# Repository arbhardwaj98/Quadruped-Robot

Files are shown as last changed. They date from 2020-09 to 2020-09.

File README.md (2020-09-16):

# Quadruped-Robot

### A Low Cost Quadruped Robot with Autonomous Capabilities

The aim was to develop a low cost quadruped robot so that it has the capability to traverse autonomously on irregular terrains:

1) The quadruped was designed employing the 5bar - 5R mechanism, allowing us to mount all the actuators on the chassis of the robot, thus minimizing the moment of inertia of the leg. 
2) Carbon Fibre Reinforced Polymer tubes were used for manufacturing the links of the mechanism to keep it feather light. By using appropriate materials and other weight reduction techniques we were able to limit the weight of the robot to 1.15 kg.
3) Stress analysis of the various mechanical components of the robot to prevent failures. Material Optimizations were implemented to reduce weight and strengthen the components.
4) ROS was integrated with the robot, after developing the URDF of the 5bar - 5R closed chain. Then ROS controllers on each of the eight actuators were set up to achieve the joint control. 
5) Stereo Camera and IMU sensors were integrated with the robot in the simulation. Extended Kalman Filtering was used for the fusion of the two sensor data to produce a much accurate odometry.
6) Equations of motion were derived for the robot A base controllers was developed to provide movement to the toe and to generate the various types of motion given the command velocity.
7) Tested using Gazebo based physics simulation for the robot, to validate the equations derived, check robot stability and to test the efficiency of the base controller.

Find more information about the robot [here](https://drive.google.com/file/d/16AhPm6JRH62gSZBvzB-JlDFh6qmGrHIq/view?usp=sharing).

Check out the [videos](https://drive.google.com/drive/folders/1-zKFX-dxUtHMzNQqa7gvRL7YORVA8Zfu?usp=sharing) of the prototype and simulation.

## Includes:

1) Description Files
2) Gazebo Simulation Package
3) ROS Control Package
4) Hardware Drivers
5) Matlab Codes for Trajectory Generation
6) CAD Files

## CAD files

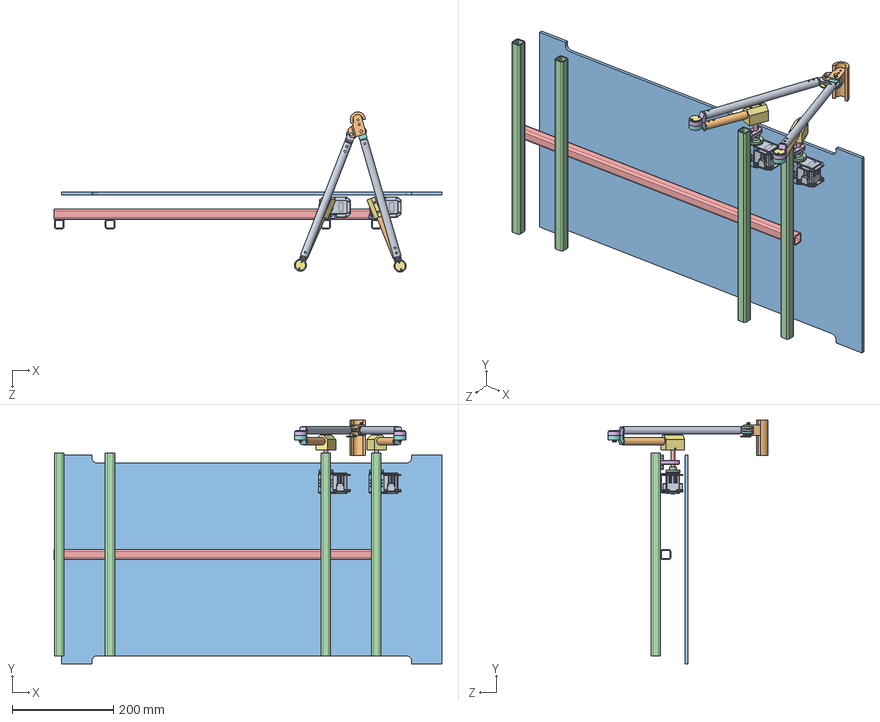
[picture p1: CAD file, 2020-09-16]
CAD/Minitaur1.4/assembly.SLDASM
764.9 x 480.8 x 315.8 mm
ncoupler x 2
ncrank x 2
Channel_2
Channel_1
joint_part_2 x 2
joint_part_3 x 4
joint_part_4 x 2
Dynamixel_64T x 2
Dynamixel_64T_servohorn x 2
Dynamixel_FR05-S101K x 2
motor_shaft_hub1 x 2
motor_shaft x 2
bearing_housing x 2
motor_shaft_hub2 x 2
joint_bottom_part_2
joint_part_1
toe

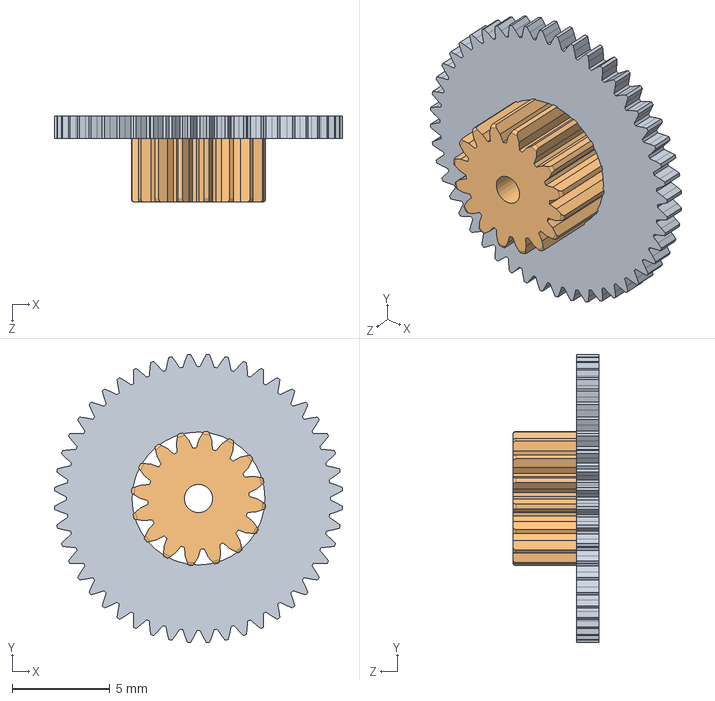
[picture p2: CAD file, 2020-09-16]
CAD/Minitaur1.4/egrane3aluminiolaton.SLDPRT.SLDASM
14.7 x 14.7 x 4.40 mm
egrane3laton
egrane3aluminio

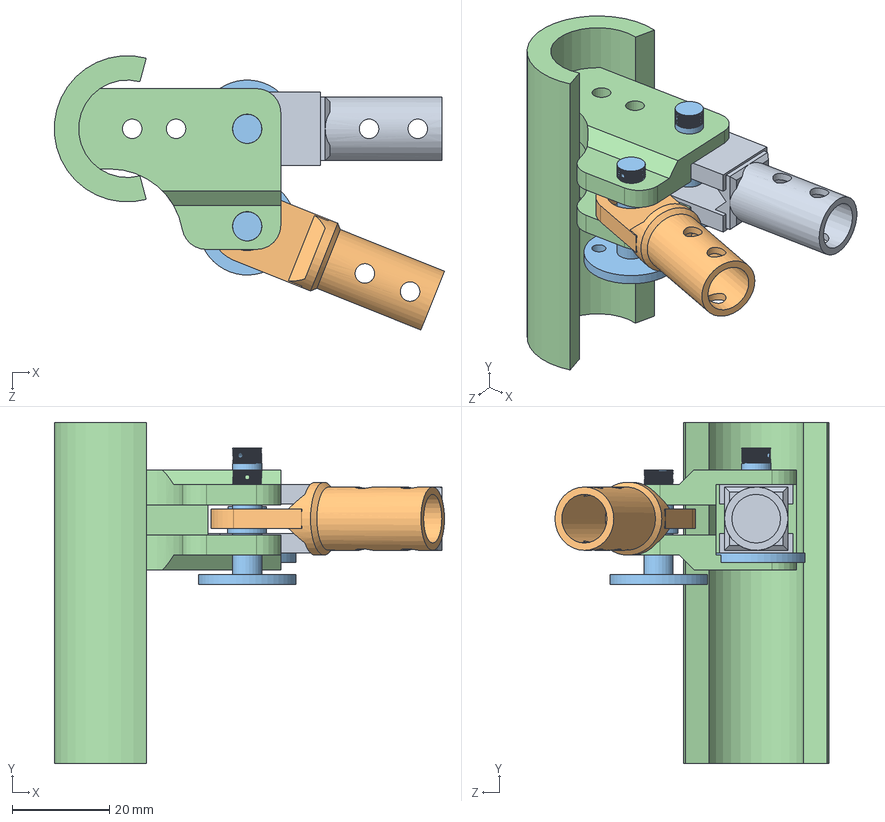
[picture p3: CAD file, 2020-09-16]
CAD/Minitaur1.4/Joint_Bottom_Assembly.SLDASM
80.0 x 70.0 x 56.2 mm
joint_bottom_part_2
joint_part_1
toe
joint_part_3

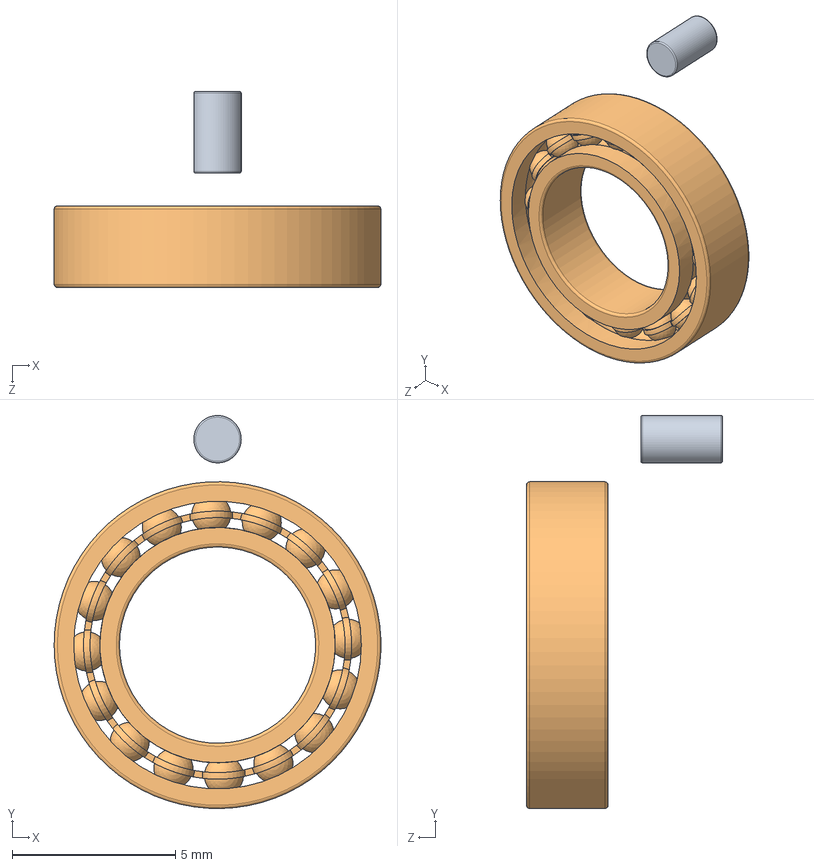
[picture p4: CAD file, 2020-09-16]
CAD/Minitaur1.4/egrane2latonpin.SLDPRT.SLDASM
10.00 x 12.0 x 6.00 mm
egrane2latonpin
radial ball bearing_68_am

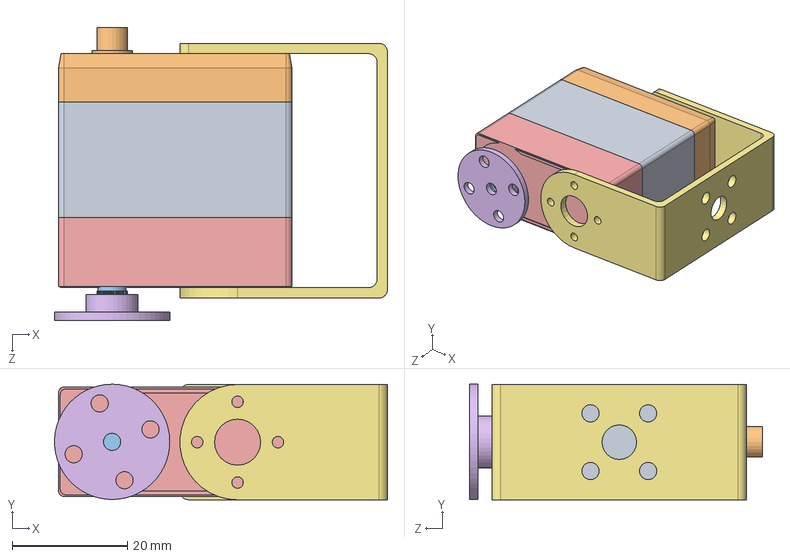
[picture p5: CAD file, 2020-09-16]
CAD/Minitaur1.4/servo.SLDASM
57.7 x 20.1 x 50.8 mm
centroservo
egrane3laton
egrane3aluminio
egrane4laton
egrane4aluminio
engrane2
pincorto
pinlargo
radial ball bearing_68_am x 2
baseservo
otro
egrane2latonpin
tapa servo
Bracket-Horn
mount

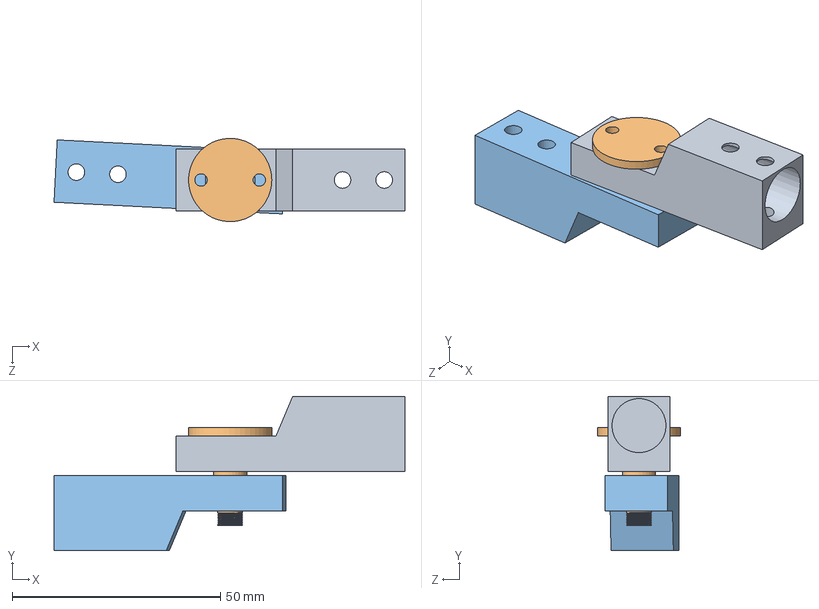
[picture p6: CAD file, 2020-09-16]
CAD/Minitaur1.4/Joint_Assembly.SLDASM
84.3 x 37.0 x 20.0 mm
joint_part_2
joint_part_3
joint_part_5

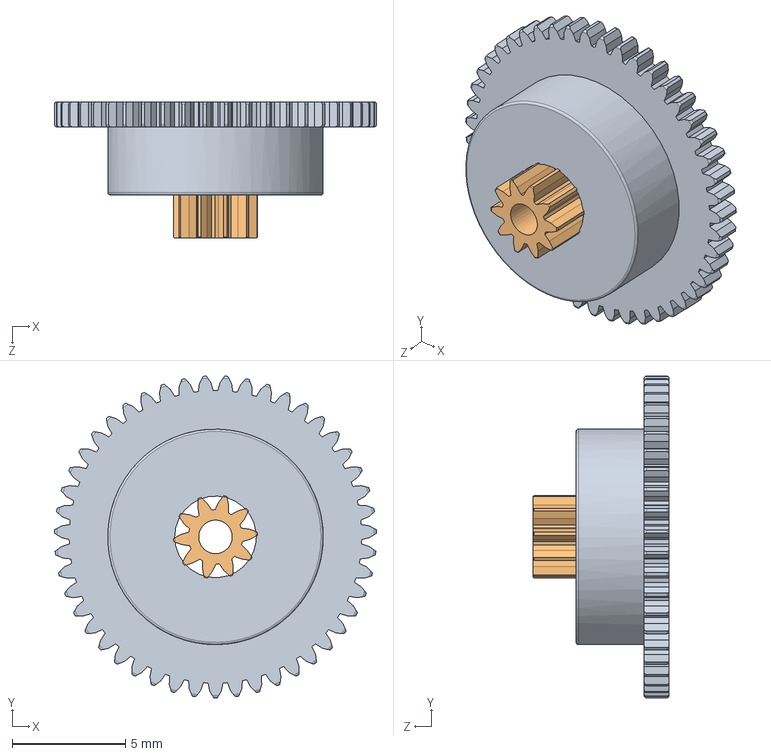
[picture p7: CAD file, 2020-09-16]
CAD/Minitaur1.4/egrane4aluminiolaton.SLDPRT.SLDASM
14.2 x 14.2 x 6.00 mm
egrane4laton
egrane4aluminio

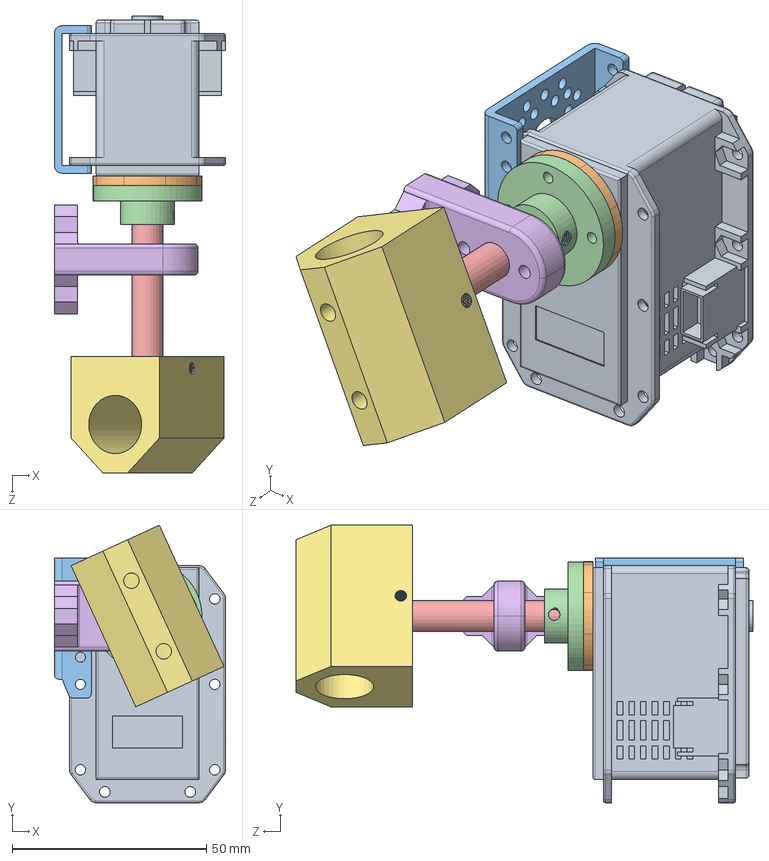
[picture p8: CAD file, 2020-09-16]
CAD/Minitaur1.4/Dynamixel_assem.SLDASM
44.1 x 71.5 x 117.7 mm
Dynamixel_64T
Dynamixel_64T_servohorn
Dynamixel_FR05-S101K
motor_shaft_hub1
motor_shaft
bearing_housing
motor_shaft_hub2

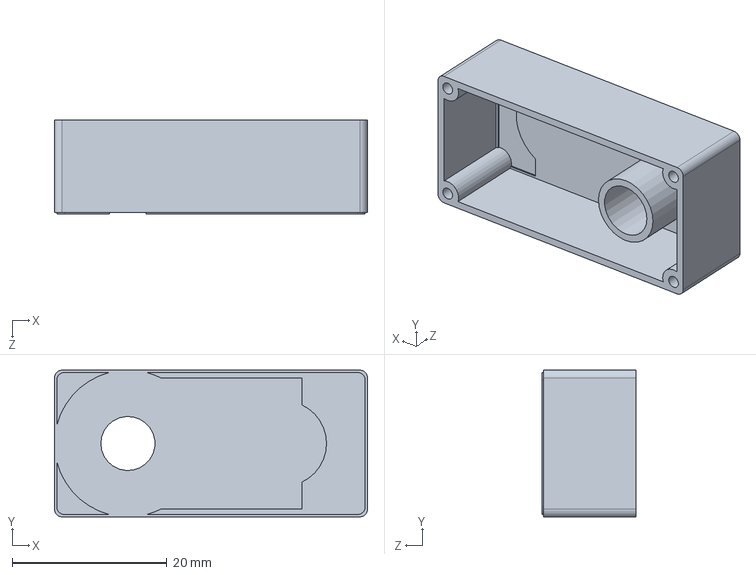
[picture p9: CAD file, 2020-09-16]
CAD/Minitaur1.4/tapa servo.SLDPRT
40.5 x 19.0 x 12.2 mm

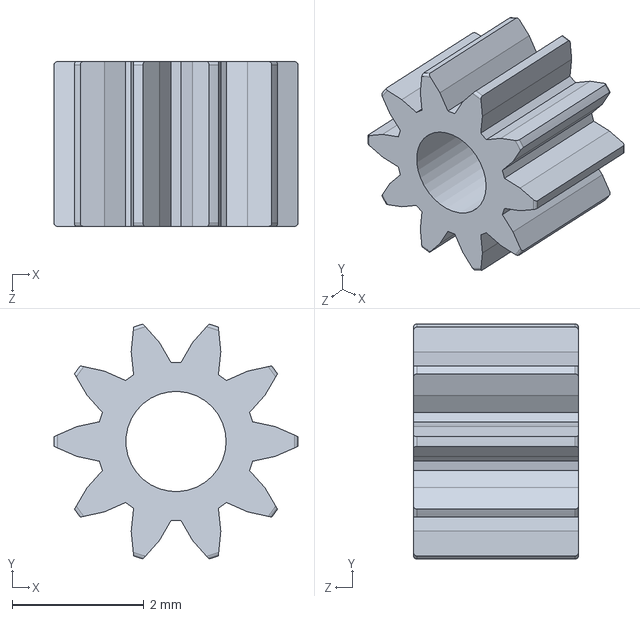
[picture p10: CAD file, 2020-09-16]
CAD/Minitaur1.4/egrane4aluminio.SLDPRT
3.70 x 3.56 x 2.50 mm

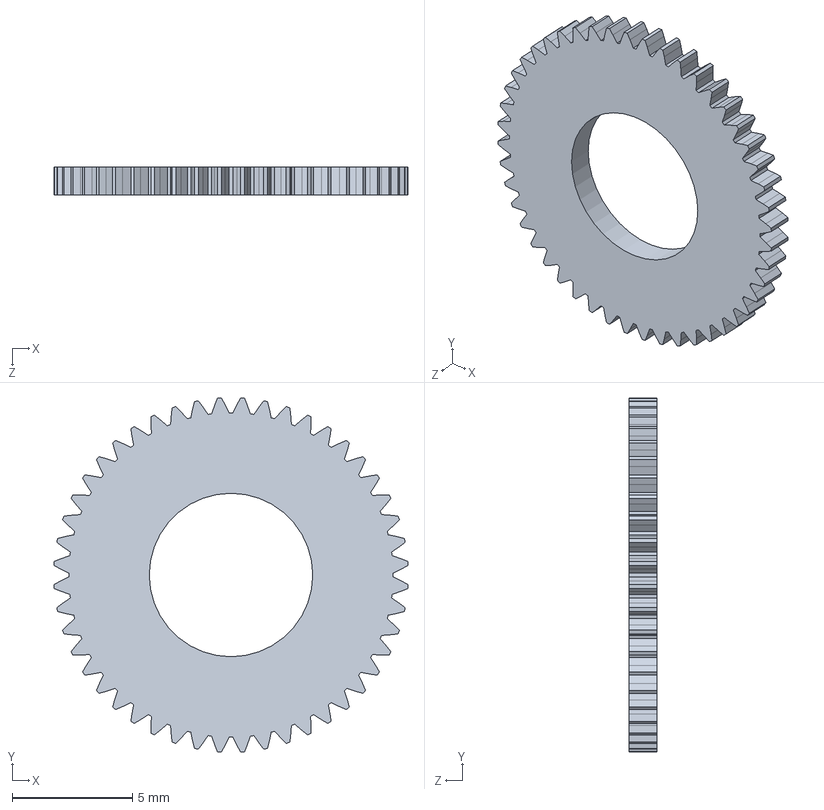
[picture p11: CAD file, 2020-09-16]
CAD/Minitaur1.4/egrane3laton.SLDPRT
14.7 x 14.7 x 1.15 mm

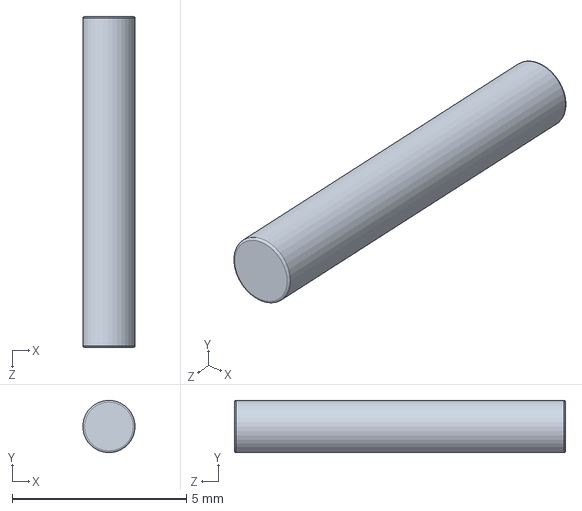
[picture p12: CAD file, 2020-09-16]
CAD/Minitaur1.4/pinlargo.SLDPRT
1.50 x 1.50 x 9.50 mm

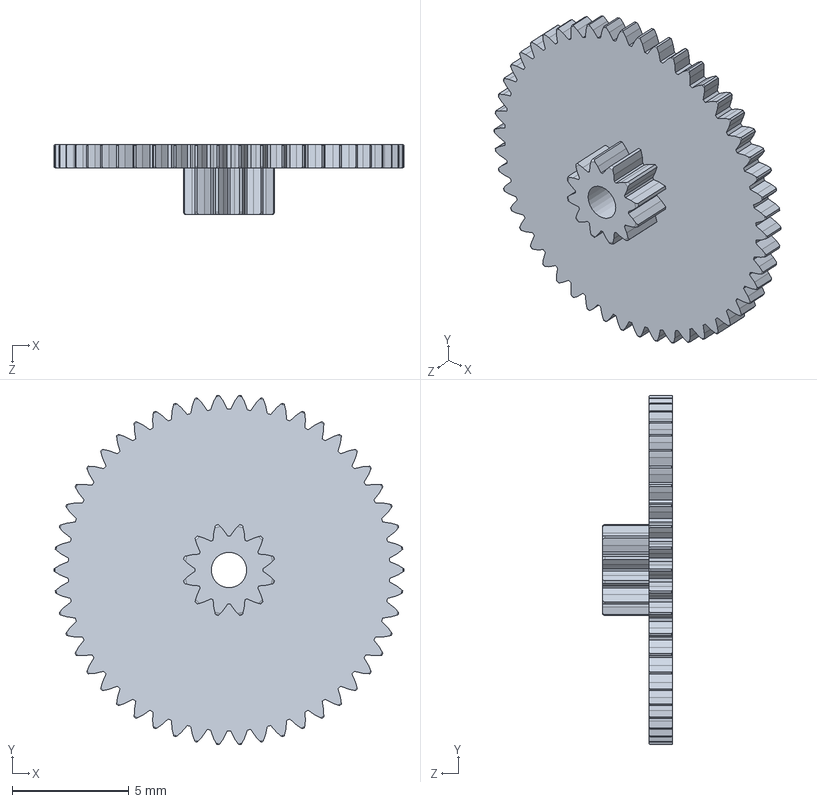
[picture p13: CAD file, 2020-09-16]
CAD/Minitaur1.4/engrane2.SLDPRT
15.0 x 15.0 x 3.00 mm

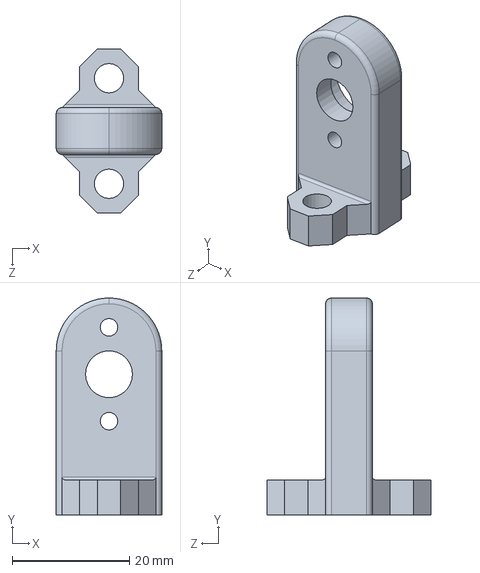
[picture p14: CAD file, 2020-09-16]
CAD/Minitaur1.4/bearing_housing.SLDPRT
18.0 x 37.0 x 28.0 mm

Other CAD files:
CAD/Minitaur1.4/MirrorJoint_Assembly.SLDASM
CAD/Minitaur1.4/joint_part_4.SLDPRT
CAD/Minitaur1.4/joint_part_2.SLDPRT
CAD/Minitaur1.4/joint_part_1.SLDPRT
CAD/Minitaur1.4/Bracket-Horn - Copy.SLDPRT
CAD/Minitaur1.4/Bracket-Horn.SLDPRT
CAD/Minitaur1.4/Channel_1.SLDPRT
CAD/Minitaur1.4/Channel_2.SLDPRT
CAD/Minitaur1.4/Dynamixel_64T.SLDPRT
CAD/Minitaur1.4/Dynamixel_64T_servohorn.SLDPRT
CAD/Minitaur1.4/Dynamixel_FR05-S101K.SLDPRT
CAD/Minitaur1.4/Mirrorjoint_part_1.SLDPRT
CAD/Minitaur1.4/Mirrorjoint_part_2.SLDPRT
CAD/Minitaur1.4/Mirrorjoint_part_3.SLDPRT
CAD/Minitaur1.4/baseservo.SLDPRT
CAD/Minitaur1.4/blue_sheet.SLDPRT
CAD/Minitaur1.4/bracket.SLDPRT
CAD/Minitaur1.4/centroservo.SLDPRT
CAD/Minitaur1.4/egrane2latonpin.SLDPRT
CAD/Minitaur1.4/egrane3aluminio.SLDPRT
CAD/Minitaur1.4/egrane4laton.SLDPRT
CAD/Minitaur1.4/joint_bottom_part_2.SLDPRT
CAD/Minitaur1.4/joint_part_3.SLDPRT
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

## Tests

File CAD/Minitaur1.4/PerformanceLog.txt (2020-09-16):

Mesh Preparation:  0 hr 0 min 0 sec
Standard solid mesh bolt head imprint and hard point processing:  0 hr 0 min 0 sec
Standard solid mesh total preparation including imprint:  0 hr 0 min 0 sec
Standard surface meshing for Solid Mesh:  0 hr 0 min 0 sec
Standard volume meshing for Solid Mesh:  0 hr 0 min 0 sec
Standard surface meshing for Solid Mesh:  0 hr 0 min 2 sec
Standard volume meshing for Solid Mesh:  0 hr 0 min 0 sec
Standard solid mesh arranging data:  0 hr 0 min 0 sec
Standard solid mesh total:  0 hr 0 min 2 sec
Beam mesh:  0 hr 0 min 0 sec
Preparing to transfer data:  0 hr 0 min 0 sec
Processing material properties:  0 hr 0 min 0 sec
Processing element groups:  0 hr 0 min 0 sec
Processing drop test gap nodes:  0 hr 0 min 0 sec
Updating thickness for shell regions:  0 hr 0 min 0 sec
Processing rconst for elements:  0 hr 0 min 0 sec
Processing egroups:  0 hr 0 min 0 sec
Transferring loads and boundary conditions:  0 hr 0 min 0 sec
Generating body pairs to check contact:  0 hr 0 min 0 sec
Generating contacts:  0 hr 0 min 0 sec
Number of Contacts: 0
Transfer SL1 data:  0 hr 0 min 0 sec
Generate more accurate contact data:  0 hr 0 min 0 sec
Number of contact data: 0
Transfer beam/joint contact data:  0 hr 0 min 0 sec
Transferring other special loads:  0 hr 0 min 0 sec
Transferring bearing loads:  0 hr 0 min 0 sec
Transferring mass elements:  0 hr 0 min 0 sec
Transferring point loads:  0 hr 0 min 0 sec
Transferring distributed beam loads:  0 hr 0 min 0 sec
Transferring rigid bodies:  0 hr 0 min 0 sec
Transferring component no penetration:  0 hr 0 min 0 sec
Writing Data:  0 hr 0 min 0 sec
Transferring analysis options:  0 hr 0 min 0 sec
Total midsurf mapping:  0 hr 0 min 0 sec

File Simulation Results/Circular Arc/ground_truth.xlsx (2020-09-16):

54.411 | 0.4890099103 | 0.1379409718 | 0.341428908 | -5.3830051e-05 | -0.005939948691 | 0.2292622886 | 0.9733465555
54.511 | 0.5075282487 | 0.14981719 | 0.3400975969 | -0.004973286535 | 0.000397756921 | 0.2336806229 | 0.9723006092
54.611 | 0.5195062176 | 0.1575890267 | 0.3429669403 | -0.004874737326 | 8.501360139e-05 | 0.2412445622 | 0.9704521064
54.711 | 0.5276516848 | 0.1547433837 | 0.3369757811 | 0.01095966386 | -0.005599889217 | 0.2427556595 | 0.97000939
54.811 | 0.5337589552 | 0.1529047762 | 0.3395917567 | 0.005786997303 | -0.008567197856 | 0.2389082043 | 0.9709871182
54.911 | 0.5387347817 | 0.1622892354 | 0.3413564012 | 0.0005599103618 | -0.01242952098 | 0.247694232 | 0.9687583604
55.011 | 0.5526689941 | 0.1667035885 | 0.3381427791 | 0.007897268905 | 0.004784001379 | 0.2468228497 | 0.969016629
55.111 | 0.5628028566 | 0.1689478808 | 0.3422487009 | 0.004892777955 | -0.003357203731 | 0.2427622093 | 0.9700676779
55.211 | 0.5694717382 | 0.1812458477 | 0.3394353436 | -0.008633509169 | 0.0006280059644 | 0.2493937244 | 0.9683634846
55.311 | 0.5792794843 | 0.1887241221 | 0.3413964195 | 0.002038302097 | -0.0042861431 | 0.2595608826 | 0.9657150835
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

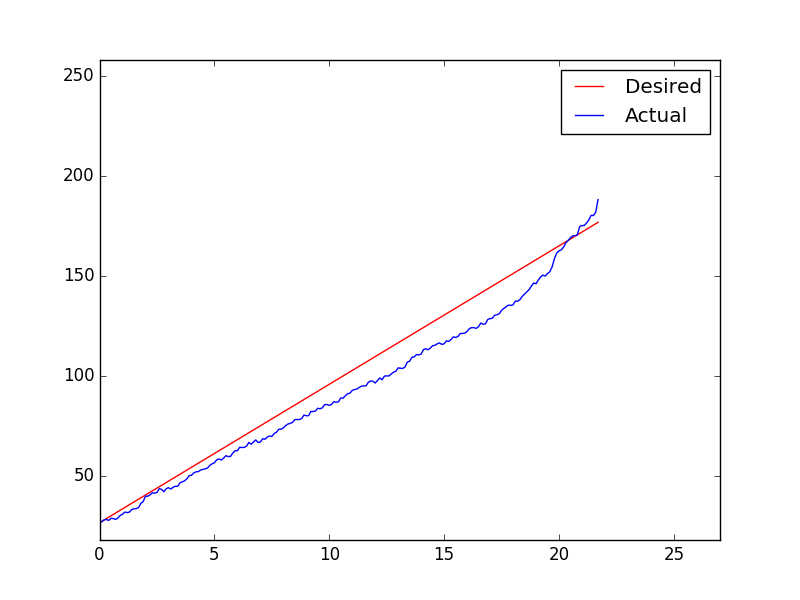
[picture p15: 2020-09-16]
Simulation Results/Circular Arc/figure_2.png

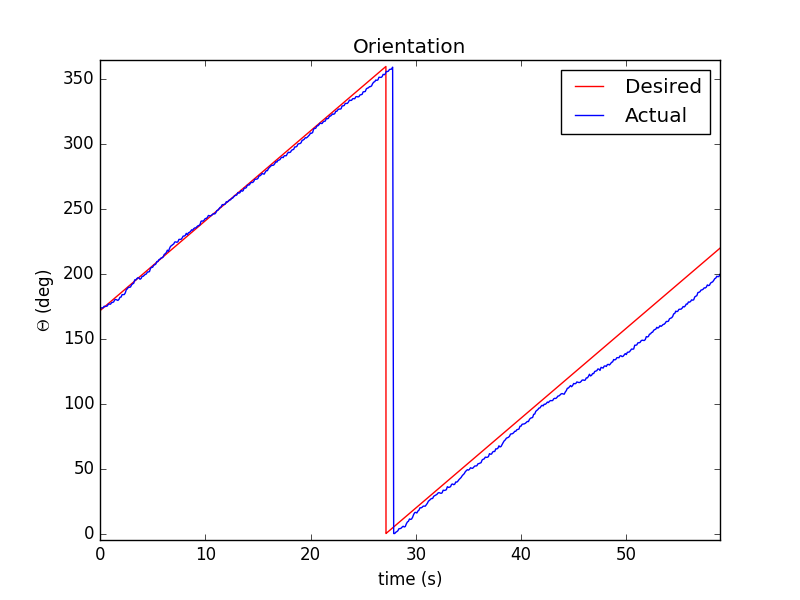
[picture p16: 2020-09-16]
Simulation Results/Circular Comp/figure_2.png

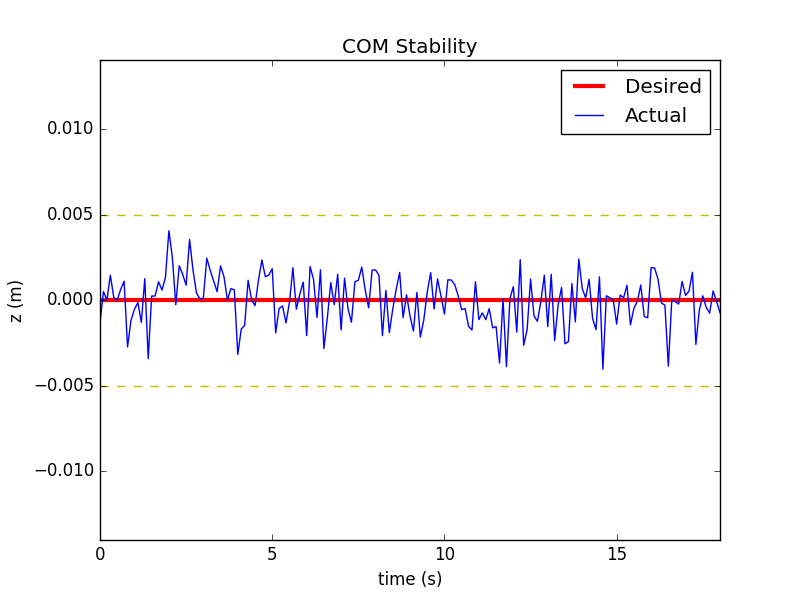
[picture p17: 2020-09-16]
Simulation Results/Straight Line/figure_3.png

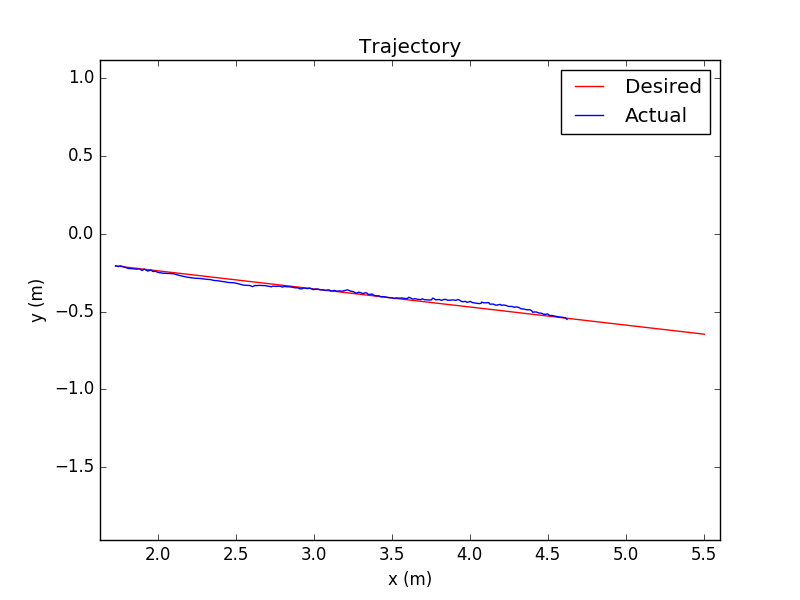
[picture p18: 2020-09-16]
Simulation Results/Straight Line/figure_1.png

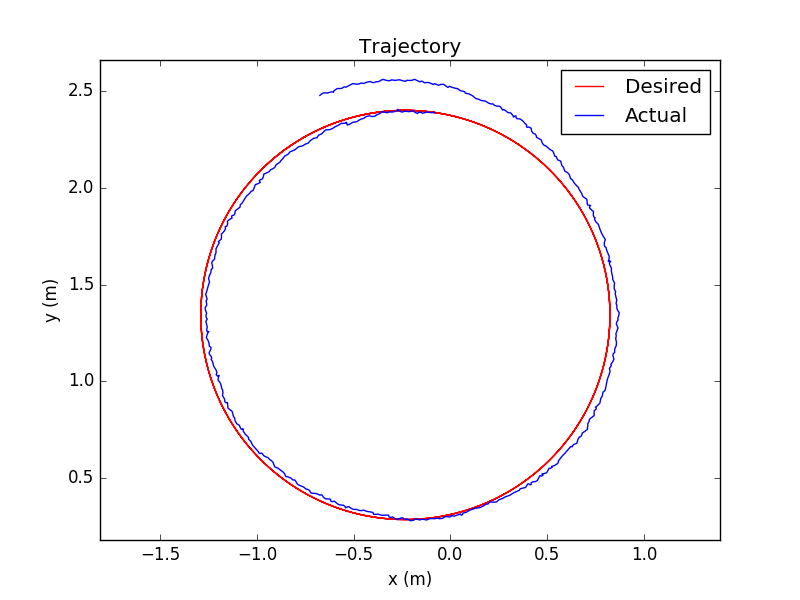
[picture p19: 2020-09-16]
Simulation Results/Circular Comp/figure_1.png

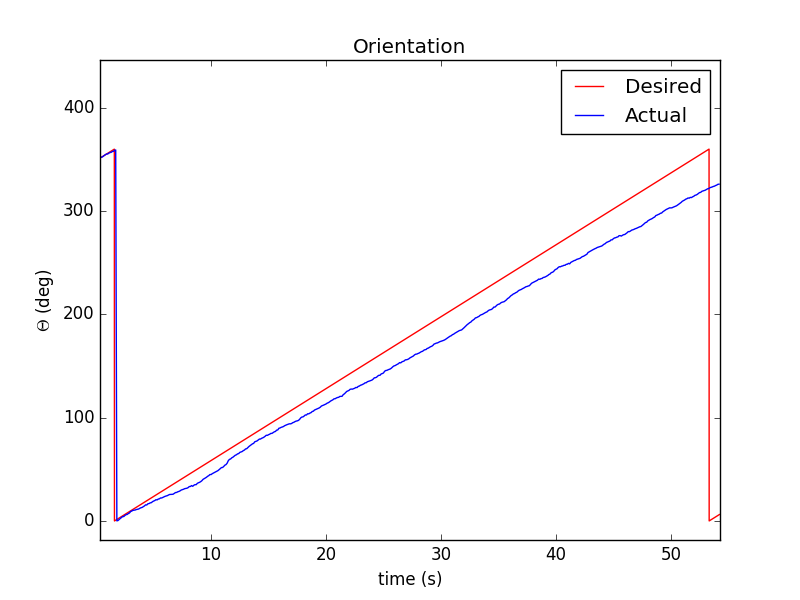
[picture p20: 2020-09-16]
Simulation Results/Rotation/figure_2.png

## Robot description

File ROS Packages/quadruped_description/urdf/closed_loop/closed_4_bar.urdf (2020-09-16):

<?xml version="1.0" ?>
<robot xmlns:xacro="http://www.ros.org/wiki/xacro" name="four_bar_split_fixed_urdf">
  <gazebo>
    <self_collide>true</self_collide>
  </gazebo>
  <link name="world"/>
  <link name="link_AB">
    <inertial>
      <origin rpy="0 0 0" xyz="-0.01 -0.15000000000000002 0"/>
      <mass value="0.07200000000000001"/>
      <inertia ixx="0.0005424000000000002" ixy="0.0" ixz="0.0" iyy="4.800000000000001e-06" iyz="0.0" izz="0.0005424000000000002"/>
    </inertial>
    <collision>
      <origin rpy="0 0 0" xyz="-0.01 -0.15000000000000002 0"/>
      <geometry>
        <box size="0.02 0.30000000000000004 0.02"/>
      </geometry>
    </collision>
    <visual>
      <origin rpy="0 0 0" xyz="-0.01 -0.15000000000000002 0"/>
      <geometry>
        <box size="0.02 0.30000000000000004 0.02"/>
      </geometry>
    </visual>
  </link>
  <gazebo reference="link_AB">
    <material>Gazebo/Wood</material>
  </gazebo>
  <link name="link_BE">
    <inertial>
      <origin rpy="0 0 0" xyz="0.05 -0.01 0"/>
      <mass value="0.024"/>
      <inertia ixx="1.6000000000000001e-06" ixy="0.0" ixz="0.0" iyy="2.0800000000000004e-05" iyz="0.0" izz="2.0800000000000004e-05"/>
    </inertial>
    <collision>
      <origin rpy="0 0 0" xyz="0.05 -0.01 0"/>
      <geometry>
        <box size="0.1 0.02 0.02"/>
      </geometry>
    </collision>
    <visual>
      <origin rpy="0 0 0" xyz="0.05 -0.01 0"/>
      <geometry>
        <box size="0.1 0.02 0.02"/>
      </geometry>
    </visual>
  </link>
  <gazebo reference="link_BE">
    <material>Gazebo/Wood</material>
  </gazebo>
  <link name="link_EC">
    <inertial>
      <origin rpy="0 0 0" xyz="-0.05 -0.01 0"/>
      <mass value="0.024"/>
      <inertia ixx="1.6000000000000001e-06" ixy="0.0" ixz="0.0" iyy="2.0800000000000004e-05" iyz="0.0" izz="2.0800000000000004e-05"/>
    </inertial>
    <collision>
      <origin rpy="0 0 0" xyz="-0.05 -0.01 0"/>
      <geometry>
        <box size="0.1 0.02 0.02"/>
      </geometry>
    </collision>
    <visual>
      <origin rpy="0 0 0" xyz="-0.05 -0.01 0"/>
      <geometry>
        <box size="0.1 0.02 0.02"/>
      </geometry>
    </visual>
  </link>
  <gazebo reference="link_EC">
    <material>Gazebo/Wood</material>
  </gazebo>
  <link name="link_CD">
    <inertial>
      <origin rpy="0 0 0" xyz="0.01 -0.15000000000000002 0"/>
      <mass value="0.07200000000000001"/>
      <inertia ixx="0.0005424000000000002" ixy="0.0" ixz="0.0" iyy="4.800000000000001e-06" iyz="0.0" izz="0.0005424000000000002"/>
    </inertial>
    <collision>
      <origin rpy="0 0 0" xyz="0.01 -0.15000000000000002 0"/>
      <geometry>
        <box size="0.02 0.30000000000000004 0.02"/>
      </geometry>
    </collision>
    <visual>
      <origin rpy="0 0 0" xyz="0.01 -0.15000000000000002 0"/>
      <geometry>
        <box size="0.02 0.30000000000000004 0.02"/>
      </geometry>
    </visual>
  </link>
  <gazebo reference="link_CD">
    <material>Gazebo/Wood</material>
  </gazebo>
  <joint name="joint_A" type="continuous">
    <origin rpy="0 0 0" xyz="0 0 0.04"/>
    <parent link="world"/>
    <child link="link_AB"/>
    <axis xyz="0 0 1"/>
  </joint>
  <joint name="joint_B" type="continuous">
    <origin rpy="0 0 0" xyz="0 -0.30000000000000004 0"/>
    <parent link="link_AB"/>
    <child link="link_BE"/>
    <axis xyz="0 0 1"/>
  </joint>
  <joint name="joint_D" type="continuous">
    <origin rpy="0 0 0" xyz="0.2 0 0.04"/>
    <parent link="world"/>
    <child link="link_CD"/>
    <axis xyz="0 0 1"/>
  </joint>
  <joint name="joint_C" type="continuous">
    <origin rpy="0 0 0" xyz="0 -0.30000000000000004 0"/>
    <parent link="link_CD"/>
    <child link="link_EC"/>
    <axis xyz="0 0 1"/>
  </joint>
  <!-- SDFormat joints -->
  <gazebo>
    <joint name="joint_E" type="fixed">
      <pose>-0.1 -0.01 0 0 0 0</pose>
      <parent>link_BE</parent>
      <child>link_EC</child>
    </joint>
  </gazebo>
</robot>

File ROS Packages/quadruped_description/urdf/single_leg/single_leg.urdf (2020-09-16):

<?xml version="1.0" ?>
<robot xmlns:xacro="http://www.ros.org/wiki/xacro" name="single_leg">

	<xacro:property name="crank_length" value="0.2"/>
	<xacro:property name="coupler_length" value="0.4"/>
	<xacro:property name="tube_width" value="0.015"/>
	<xacro:property name="motor_sep" value="0.1"/>

  <gazebo>
    <self_collide>true</self_collide>
  </gazebo>
  
  <link name = "world"/>
  <link name = "dummy_link"/>
  
  <link name="crank1">
    <inertial>
      <origin rpy="0 0 0" xyz="${crank_length/2.0} 0 0"/>
      <mass value="0.072"/>
      <inertia ixx="4.8e-06" ixy="0.0" ixz="0.0" iyy="0.0005424" iyz="0.0" izz="0.0005424"/>
    </inertial>
    <collision>
      <origin rpy="0 0 0" xyz="${crank_length/2.0} 0 0"/>
      <geometry>
        <box size="${crank_length} ${tube_width} ${tube_width}"/>
      </geometry>
    </collision>
    <visual>
      <origin rpy="0 0 0" xyz="${crank_length/2.0} 0 0"/>
      <geometry>
        <box size="${crank_length} ${tube_width} ${tube_width}"/>
      </geometry>
    </visual>
  </link>
  
  <link name="crank2">
    <inertial>
      <origin rpy="0 0 0" xyz="${crank_length/2.0} 0 0"/>
      <mass value="0.072"/>
      <inertia ixx="4.8e-06" ixy="0.0" ixz="0.0" iyy="0.0005424" iyz="0.0" izz="0.0005424"/>
    </inertial>
    <collision>
      <origin rpy="0 0 0" xyz="${crank_length/2.0} 0 0"/>
      <geometry>
        <box size="${crank_length} ${tube_width} ${tube_width}"/>
      </geometry>
    </collision>
    <visual>
      <origin rpy="0 0 0" xyz="${crank_length/2.0} 0 0"/>
      <geometry>
        <box size="${crank_length} ${tube_width} ${tube_width}"/>
      </geometry>
    </visual>
  </link>
  
  <link name="coupler1">
    <inertial>
      <origin rpy="0 0 0" xyz="${coupler_length/2.0} 0 0"/>
      <mass value="0.144"/>
      <inertia ixx="9.6e-06" ixy="0.0" ixz="0.0" iyy="0.0021696" iyz="0.0" izz="0.0021696"/>
    </inertial>
    <collision>
      <origin rpy="0 0 0" xyz="${coupler_length/2.0} 0 0"/>
      <geometry>
        <box size="${coupler_length} ${tube_width} ${tube_width}"/>
      </geometry>
    </collision>
    <visual>
      <origin rpy="0 0 0" xyz="${coupler_length/2.0} 0 0"/>
      <geometry>
        <box size="${coupler_length} ${tube_width} ${tube_width}"/>
      </geometry>
    </visual>
  </link>
  
  <link name="coupler2">
    <inertial>
      <origin rpy="0 0 0" xyz="${coupler_length/4.0} 0 0"/>
      <mass value="0.072"/>
      <inertia ixx="4.8e-06" ixy="0.0" ixz="0.0" iyy="0.0005424" iyz="0.0" izz="0.0005424"/>
    </inertial>
    <collision>
      <origin rpy="0 0 0" xyz="${coupler_length/4.0} 0 0"/>
      <geometry>
        <box size="${coupler_length/2.0} ${tube_width} ${tube_width}"/>
      </geometry>
    </collision>
    <visual>
      <origin rpy="0 0 0" xyz="${coupler_length/4.0} 0 0"/>
      <geometry>
        <box size="${coupler_length/2.0} ${tube_width} ${tube_width}"/>
      </geometry>
    </visual>
  </link>
  
  <link name="toe_extension">
    <inertial>
      <origin rpy="0 0 0" xyz="${coupler_length/4.0} 0 0"/>
      <mass value="0.072"/>
      <inertia ixx="4.8e-06" ixy="0.0" ixz="0.0" iyy="0.0005424" iyz="0.0" izz="0.0005424"/>
    </inertial>
    <collision>
      <origin rpy="0 0 0" xyz="${coupler_length/4.0} 0 0"/>
      <geometry>
        <box size="${coupler_length/2.0} ${tube_width} ${tube_width}"/>
      </geometry>
    </collision>
    <visual>
      <origin rpy="0 0 0" xyz="${coupler_length/4.0} 0 0"/>
      <geometry>
        <box size="${coupler_length/2.0} ${tube_width} ${tube_width}"/>
      </geometry>
    </visual>
  </link>
  
  
  
  <!-- joints -->
  <joint name="motor_1" type="continuous">
    <origin rpy="0 0 0" xyz="${motor_sep/2.0} 0 0.1"/>
    <parent link="world"/>
    <child link="crank1"/>
    <dynamics damping="1.0" friction="0.4"/>
    <axis xyz="0 0 1"/>
  </joint>
  <joint name="motor_2" type="continuous">
    <origin rpy="0 0 ${pi}" xyz="${-1*motor_sep/2.0} 0 0.1"/>
    <parent link="world"/>
    <child link="crank2"/>
    <dynamics damping="1.0" friction="0.4"/>
    <axis xyz="0 0 1"/>
  </joint>
  <joint name="joint_cc1" type="continuous">
    <origin rpy="0 0 -${pi-acos((crank_length+motor_sep/2.0)/coupler_length)}" xyz="${crank_length} 0 0"/>
    <parent link="crank1"/>
    <child link="coupler1"/>
    <axis xyz="0 0 1"/>
  </joint>
  <joint name="joint_cc2" type="continuous">
    <origin rpy="0 0 ${pi-acos((crank_length+motor_sep/2.0)/coupler_length)}" xyz="${crank_length} 0 0"/>
    <parent link="crank2"/>
    <child link="coupler2"/>
    <axis xyz="0 0 1"/>
  </joint>
  <joint name="joint_toe" type="continuous">
    <origin rpy="0 0 ${2*asin((crank_length+motor_sep/2.0)/coupler_length)-pi}" xyz="${coupler_length} 0 0"/>
    <parent link="coupler1"/>
    <child link="toe_extension"/>
    <axis xyz="0 0 1"/>
  </joint>
  <joint name="joint_dummy" type="fixed">
    <origin rpy="0 0 ${2*asin((crank_length+motor_sep/2.0)/coupler_length)-pi}" xyz="${coupler_length} 0 0"/>
    <parent link="coupler1"/>
    <child link="dummy_link"/>
  </joint>
  
  
  <!-- SDFormat joints -->
  <gazebo>
    <joint name="joint_fixed" type="fixed">
      <pose>${coupler_length/2.0} 0 0 0 ${pi} 0</pose>
      <parent>coupler2</parent>
      <child>toe_extension</child>
    </joint>
  </gazebo>
  
  
  
  <!-- transmission elements -->
  <transmission name="motor_1_transmission">
	<type>transmission_interface/SimpleTransmission</type>
	<joint name="motor_1">
	  <hardwareInterface>hardware_interface/EffortJointInterface</hardwareInterface>
	</joint>
	<actuator name="motor_1_dynamixel">
	  <mechanicalReduction>1</mechanicalReduction>
	  <hardwareInterface>hardware_interface/EffortJointInterface</hardwareInterface>
	</actuator>
  </transmission>
  
  <transmission name="motor_2_transmission">
	<type>transmission_interface/SimpleTransmission</type>
	<joint name="motor_2">
	  <hardwareInterface>hardware_interface/EffortJointInterface</hardwareInterface>
	</joint>
	<actuator name="motor_2_dynamixel">
	  <mechanicalReduction>1</mechanicalReduction>
	  <hardwareInterface>hardware_interface/EffortJointInterface</hardwareInterface>
	</actuator>
  </transmission>
  
  
  <!-- Control Plugin -->
  <gazebo>
  	<plugin name="gazebo_ros_control" filename="libgazebo_ros_control.so">
      <robotNamespace>single_leg</robotNamespace>
      <robotSimType>gazebo_ros_control/DefaultRobotHWSim</robotSimType>
      <legacyModeNS>true</legacyModeNS>
  	</plugin>			
	<self_collide>true</self_collide>	  	
  </gazebo>
  
  <gazebo>
    <plugin name="p3d_base_pose" filename="libgazebo_ros_p3d.so">
	  <robotNamespace>/single_leg</robotNamespace>
	  <updateRate>10.0</updateRate>
	  <bodyName>dummy_link</bodyName>
      <topicName>base_pose_ground_truth</topicName>
      <frameName>world</frameName>
	</plugin>
  </gazebo>
  
  
  
</robot>

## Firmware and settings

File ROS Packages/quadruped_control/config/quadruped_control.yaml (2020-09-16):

quadruped:
  # Publish all joint states -----------------------------------
  joint_state_controller:
    type: joint_state_controller/JointStateController
    publish_rate: 50

  # Position Controllers ---------------------------------------
  leg1_motor_1_position_controller:
    type: effort_controllers/JointPositionController
    joint: leg1_motor_1
    pid: {p: 10.0, i: 0.01, d: 1}
  leg1_motor_2_position_controller:
    type: effort_controllers/JointPositionController
    joint: leg1_motor_2
    pid: {p: 10.0, i: 0.01, d: 1}
  leg2_motor_1_position_controller:
    type: effort_controllers/JointPositionController
    joint: leg2_motor_1
    pid: {p: 10.0, i: 0.01, d: 1}
  leg2_motor_2_position_controller:
    type: effort_controllers/JointPositionController
    joint: leg2_motor_2
    pid: {p: 10.0, i: 0.01, d: 1}
  leg3_motor_1_position_controller:
    type: effort_controllers/JointPositionController
    joint: leg3_motor_1
    pid: {p: 10.0, i: 0.01, d: 1}
  leg3_motor_2_position_controller:
    type: effort_controllers/JointPositionController
    joint: leg3_motor_2
    pid: {p: 10.0, i: 0.01, d: 1}
  leg4_motor_1_position_controller:
    type: effort_controllers/JointPositionController
    joint: leg4_motor_1
    pid: {p: 10.0, i: 0.01, d: 1}
  leg4_motor_2_position_controller:
    type: effort_controllers/JointPositionController
    joint: leg4_motor_2
    pid: {p: 10.0, i: 0.01, d: 1}

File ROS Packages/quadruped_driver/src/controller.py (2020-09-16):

#!/usr/bin/env python

import numpy as np
import matplotlib.pyplot as plt
import rospy
import os
import numpy as np
import sys, tty, termios
import math
import time
from geometry_msgs.msg import Twist
from dynamixel_sdk import *

'''



                 m1 |-------------------| m1
          Leg1      |     F R O N T     |      Leg3              /|\ x
                 m2 |                   | m2                      |
                    |                   |                         |
                    |                   |                  <----- o
                  RIGHT                LEFT                y
                    |                   |
                    |                   |
                 m1 |                   | m1
          Leg2      |      B A C K      |      Leg4
                 m2 |-------------------| m2



'''

    # ..... Geometrical .....
r1              = 20.0               # length of Cranks
r2              = 40.0               # length of Coupler Links
L               = 5.0                # Distance between the pivot points
base_l          = 35.0               # Base length
base_w          = 60.0               # Base width
d               = 0.0                # Offset distance between side edge and foot center
xc1 =  L/2.0; yc1 = 0.0              # Joint-1 coordinates
xc2 = -L/2.0; yc2 = 0.0              # Joint-2 coordinates

    # ..... Trajectory .....
stroke_h        = 18.0               # Robot Height
ht              = 6.0                # Step height

    # ..... Temporal .....
def_period      = 1.0                # default period
dc              = 0.8                # Duty factor
dt              = 0.03               # Extension time
phi1            = +0.5               # Phase diff. b/w Contralateral legs (Leg 1 and Leg 4, Leg 2 and Leg 3)
phi2            = +0.75              # Phase diff. b/w Ipsilateral legs  (Leg 1 and Leg 3, Leg 2 and Leg 4)
step_size       = 0.002
n               = 0
transn_idx      = 0

leg_phase       = np.array([0, 0.5, 0.25, 0.75], dtype=float)

# Control table address
ADDR_MX_TORQUE_ENABLE       = 24
ADDR_MX_GOAL_POSITION       = 30
ADDR_MX_MOVING_SPEED        = 32
ADDR_MX_PRESENT_POSITION    = 36
ADDR_MX_PRESENT_SPEED       = 38

# Protocol version
PROTOCOL_VERSION            = 1.0               # See which protocol version is used in the Dynamixel

# Data Byte Length
LEN_MX_GOAL_POSITION        = 2
LEN_MX_PRESENT_POSITION     = 2
LEN_MX_MOVING_SPEED         = 2
LEN_MX_PRESENT_SPEED        = 2

# Default setting
BAUDRATE                    = 1000000             # Dynamixel default baudrate : 57600
DEVICENAME                  = '/dev/ttyUSB0'      # Check which port is being used on your controller


TORQUE_ENABLE               = 1               # Value for enabling the torque
TORQUE_DISABLE              = 0               # Value for disabling the torque
DXL_MINIMUM_POSITION_VALUE  = 0               # Dynamixel will rotate between this value
DXL_MAXIMUM_POSITION_VALUE  = 4095            # and this value
DXL_MOVING_STATUS_THRESHOLD = 2               # Dynamixel moving status threshold

NUM_MOTORS                  = 8
NUM_LEGS                    = 4
MOTOR_AXIS                  = np.ones(8, dtype=int)
MOTOR_OFFSETS               = np.array([2048 for i in range(NUM_MOTORS)],dtype=int)
JOINT_LIMITS                = np.array([[0,4095],[0,4095]])

prev_vel        = Twist()
curr_vel        = Twist()
reso_ang        = 0.01
reso_lin        = 0.001
isChanged       = False
isReceived      = 4
motor_angles    = np.zeros(8)
leg_offset      = np.array((leg_phase/step_size),dtype=int)


#motor_handler   = HandlerClass()


class HandlerClass:

    portHandler = None
    packetHandler = None

    def __init__(self):
        self.get_port_handler()
        self.packetHandler = PacketHandler(PROTOCOL_VERSION)

    def get_port_handler(self):
        self.portHandler = PortHandler(DEVICENAME)

        if self.portHandler.openPort():
            print("Succeeded to open the port")
        else:
            print("Failed to open the port")
            quit()

        if self.portHandler.setBaudRate(BAUDRATE):
            print("Succeeded to change the baudrate")
        else:
            print("Failed to change the baudrate")
            quit()

    def close_port(self):
        self.portHandler.closePort()


def setup_motors():
    check_connection()
    write_torque(TORQUE_ENABLE)

def check_connection():
    isConnected = True
    for i in range(NUM_MOTORS):
        id = i+1
        status = check_motor(id)
        if not status:
            isConnected = False
            print("Cannot communicate with motor id: %d"% (id))
    if not isConnected:
        print("Cannot communicate with all the motors")
        print("Cannot start base controller")
        exit(1)

def check_motor(id):
    val = True
    dxl_model_number, dxl_comm_result, dxl_error = motor_handler.packetHandler.ping(motor_handler.portHandler, id)
    if dxl_comm_result != COMM_SUCCESS:
        print("%s" % motor_handler.packetHandler.getTxRxResult(dxl_comm_result))
        val = False
    elif dxl_error != 0:
        print("%s" % motor_handler.packetHandler.getRxPacketError(dxl_error))
        val = False
    else:
        print("[ID:%03d] ping Succeeded. Dynamixel model number : %d" % (id, dxl_model_number))

    return val

def write_torque(character):
    for i in range(NUM_MOTORS):
        id = i+1
        dxl_comm_result, dxl_error = motor_handler.packetHandler.write1ByteTxRx(motor_handler.portHandler, id, ADDR_MX_TORQUE_ENABLE, character)
        if dxl_comm_result != COMM_SUCCESS:
            print("%s" % motor_handler.packetHandler.getTxRxResult(dxl_comm_result))
        elif dxl_error != 0:
            print("%s" % motor_handler.packetHandler.getRxPacketError(dxl_error))
        else:
            print("Dynamixel#%d has been successfully connected" % id)

def write_motor_angles():
    goal_pos = get_goal_pos()
    execute_goal_pos(goal_pos)

def get_goal_pos():
    goal_pos = 2048*motor_angles/np.pi
    goal_pos = goal_pos*MOTOR_AXIS + MOTOR_OFFSETS
    goal_pos = np.array(goal_pos, dtype=int)

    return goal_pos

def move_motors():
    goal_pos_steps = get_goal_steps()
    for goal_pos in goal_pos_steps:
        execute_goal_pos(goal_pos)
        time.sleep(0.1)

def get_goal_steps():
    num_steps = 10
    goal_pos_steps  = []

    current_pos = get_current_pose()
    goal_pos = 2048*motor_angles/np.pi
    goal_pos = goal_pos*MOTOR_AXIS + MOTOR_OFFSETS
    diff_step = (goal_pos-current_pos)/num_steps
    diff_step.astype(int)

    for i in range(num_steps):
        goal_pos_steps.append(current_pos + (i+1)*diff_step)
    return goal_pos_steps

def get_current_pose():
    pos = np.zeros((NUM_MOTORS),dtype=int)
    for i in range(NUM_MOTORS):
        id = i+1
        dxl_present_position, dxl_comm_result, dxl_error = motor_handler.packetHandler.read2ByteTxRx(motor_handler.portHandler, id, ADDR_MX_PRESENT_POSITION)
        if dxl_comm_result != COMM_SUCCESS:
            print("%s" % motor_handler.packetHandler.getTxRxResult(dxl_comm_result))
        elif dxl_error != 0:
            print("%s" % motor_handler.packetHandler.getRxPacketError(dxl_error))

        pos[i] = dxl_present_position
        #print("[ID:%03d] PresPos:%d" % (id, dxl_present_position))

    return pos

def calculate_speeds(goal, current, time):
    diff = np.absolute((goal - current), dtype=float)
    speeds = diff/time
    speeds = np.array(speeds,dtype=int)
    return speeds

def set_moving_speeds(speeds): #yahan se
    groupSyncWrite = GroupSyncWrite(motor_handler.portHandler, motor_handler.packetHandler, ADDR_MX_MOVING_SPEED, LEN_MX_MOVING_SPEED)
    param_moving_speeds_i = [0, 0]
    # Allocate moving speed value into byte array
    for i in range(NUM_MOTORS):
        param_moving_speeds_i = [DXL_LOBYTE(DXL_LOWORD(speeds[i])), DXL_HIBYTE(DXL_LOWORD(speeds[i]))]
        id = i+1
        dxl_addparam_result = groupSyncWrite.addParam(id, param_moving_speeds_i)
        if dxl_addparam_result != True:
            print("[ID:%03d] groupSyncWrite addparam failed" % id)
            quit()

    dxl_comm_result = groupSyncWrite.txPacket()
    if dxl_comm_result != COMM_SUCCESS:
        print("%s" % motor_handler.packetHandler.getTxRxResult(dxl_comm_result))
    else:
        print("Moving speeds have been successfully written")

    # Clear syncwrite parameter storage
    groupSyncWrite.clearParam()
    return True

def execute_goal_pos(goal):
    groupSyncWrite = GroupSyncWrite(motor_handler.portHandler, motor_handler.packetHandler, ADDR_MX_GOAL_POSITION, LEN_MX_GOAL_POSITION)
    param_goal_positions = [0, 0]
    # Add Dynamixel moving speed value to the Syncwrite parameter storage
    for i in range(NUM_MOTORS):
        id = i+1
        param_goal_positions_i = [DXL_LOBYTE(DXL_LOWORD(goal[i])), DXL_HIBYTE(DXL_LOWORD(goal[i]))]
        #print("Dynamixel#%d goal pos: %d" % (id, pos[id-1]))
        dxl_addparam_result = groupSyncWrite.addParam(id, param_goal_positions_i)
        if dxl_addparam_result != True:
            print("[ID:%03d] groupSyncWrite addparam failed" % id)
            quit()

    dxl_comm_result = groupSyncWrite.txPacket()
    if dxl_comm_result != COMM_SUCCESS:
        print("%s" % handler.packetHandler.getTxRxResult(dxl_comm_result))

        #print("Goal positions have been successfully written")

    # Clear syncwrite parameter storage
    groupSyncWrite.clearParam()
    return True

def write_address(address, val, id):
    dxl_comm_result, dxl_error = motor_handler.packetHandler.write2ByteTxRx(motor_handler.portHandler, id, address, val)
    if dxl_comm_result != COMM_SUCCESS:
        print("%s" % motor_handler.packetHandler.getTxRxResult(dxl_comm_result))
    elif dxl_error != 0:
        print("%s" % motor_handler.packetHandler.getRxPacketError(dxl_error))

    return (dxl_comm_result == COMM_SUCCESS)


def getParams():
    global n
    global transn_idx

    lin_vel = 100*curr_vel.linear.x
    ang_vel = curr_vel.angular.z

    #params = [stroke, ht, period]
    l_params = np.zeros(3)
    r_params = np.zeros(3)

    vl = lin_vel - base_w*ang_vel/2
    vr = lin_vel + base_w*ang_vel/2

    if abs(vl) > reso_lin:
        l_params[0] = dc*def_period*vl
        l_params[1] = (2.5*abs(l_params[0])/8 + 1)
    if abs(vr) > reso_lin:
        r_params[0] = dc*def_period*vr
        r_params[1] = (2.5*abs(r_params[0])/8 + 1)

    l_params[2] = def_period
    r_params[2] = def_period

    n = int(def_period/step_size)
    transn_idx = (n-leg_offset)%n

    return [l_params, r_params]

def getTrajectory(paramTraj):
    stroke, ht, period = paramTraj

    C_x = np.array([              - (stroke/2) - (dt*stroke)/(dc*period),
                                                    - stroke/(dc*period),
                      (3*stroke)/(dc*pow((2*dt - period + dc*period),2)),
                     (2*stroke)/(dc*pow((2*dt - period + dc*period),3))],
                                                             dtype=float)

    C_y = np.array([                               -stroke_h,
                                                           0,
                            (16*ht)/pow((period*(dc - 1)),2),
                            (32*ht)/pow((period*(dc - 1)),3),
                           (16*ht)/pow((period*(dc - 1)),4)],
                                                 dtype=float)


    Time = np.arange(0,period,step_size)
    X = np.zeros(n); Y = np.zeros(n)

    #.......... X vs Time ..........#
    Phase_x = np.array([((0.5*dc*period+dt)/step_size), ((period-(dt+0.5*dc*period))/step_size)], dtype=int)
    X[0:Phase_x[0]] = -stroke*Time[0:Phase_x[0]]/(dc*period)
    t = Time[Phase_x[0]:Phase_x[1]] - (0.5*dc*period+dt)
    X[Phase_x[0]:Phase_x[1]] = np.dot((np.vstack((np.ones(t.size), t, np.power(t,2), np.power(t,3))).T),C_x)
    X[Phase_x[1]:] = stroke*(period - Time[Phase_x[1]:])/(dc*period)

    #.......... Y vs Time ..........#
    Phase_y = np.array([(0.5*dc*period)/step_size, ((1 - 0.5*dc)*period)/step_size], dtype=int)
    Y[0:Phase_y[0]] = -1*stroke_h*np.ones(Phase_y[0])
    t = Time[Phase_y[0]:Phase_y[1]] - (0.5*dc*period)
    Y[Phase_y[0]:Phase_y[1]] = np.dot((np.vstack((np.ones(t.size), t, np.power(t,2), np.power(t,3), np.power(t,4))).T),C_y)
    Y[Phase_y[1]:] = -1*stroke_h*np.ones(n-Phase_y[1])

    #return np.column_stack((X, Y, Time))
    return [X, Y, Time]

def subplotTraj(x,y,idx,name):
    plt.subplot(idx)
    plt.plot(x, y);
    plt.title(name);

def plotTraj(X_l, Y_l, Time_l, X_r, Y_r, Time_r):
    subplotTraj(Time_l, X_l, 231, 'Left X vs Time')
    subplotTraj(Time_l, Y_l, 232, 'Left Y vs Time')
    subplotTraj(X_l, Y_l, 233, 'Left Trajectory')

    subplotTraj(Time_r, X_r, 234, 'Right X vs Time')
    subplotTraj(Time_r, Y_r, 235, 'Right Y vs Time')
    subplotTraj(X_r, Y_r, 236, 'Right Trajectory')

    plt.show()

def solveIK(x,y):
    a_sq = np.power((x - xc1),2) + np.power((y - yc1),2);
    b_sq = np.power((x - xc2),2) + np.power((y - yc2),2);
    a = np.sqrt(a_sq)
    b = np.sqrt(b_sq)

    o1 = np.arccos((-(r2*r2) + (r1*r1) + b_sq)/(2*r1*b));
    o2 = np.arccos((-(r2*r2) + (r1*r1) + a_sq)/(2*r1*a));
    g1 = np.arccos(-(a_sq - (L*L) - b_sq)/(2*L*b));
    g2 = np.arccos(-(b_sq - (L*L) - a_sq)/(2*L*a));
    Q2 = -(g1+o1);
    Q1 = -(np.pi-(g2+o2));

    return [Q1, Q2]

def saveData(pos, var):
    np.savetxt(pos, var, delimiter=",")

def cmd_vel_listener():
    global curr_vel
    rospy.init_node('base_controller', anonymous=True)
    curr_vel = rospy.wait_for_message("cmd_vel", Twist, timeout=None)
    rospy.Subscriber("cmd_vel", Twist, callback)

def callback(data):
    global prev_vel
    global curr_vel
    global isChanged
    curr_vel = data
    if abs(curr_vel.linear.x - prev_vel.linear.x) > reso_lin or abs(curr_vel.angular.z - prev_vel.angular.z) > reso_ang:
        prev_vel = curr_vel
        isChanged = True

def solver():
    l_params, r_params = getParams()
    [X_l, Y_l, Time_l] = getTrajectory(l_params)
    [X_r, Y_r, Time_r] = getTrajectory(r_params)
    print(l_params)
    print(r_params)
    #plotTraj(X_l, Y_l, Time_l, X_r, Y_r, Time_r)
    [Q1_l, Q2_l] = solveIK(X_l,Y_l)
    [Q1_r, Q2_r] = solveIK(X_r,Y_r)

    return [Q1_l, Q2_l, Q1_r, Q2_r]

def change_motion_plan(idx_t, motion_plan, new_motion_plan):
    global isReceived
    isReceived = isReceived + 1
    if idx_t == transn_idx[0]: motion_plan[0] = new_motion_plan[0]
    elif idx_t == transn_idx[1]: motion_plan[1] = new_motion_plan[1]
    elif idx_t == transn_idx[2]: motion_plan[2] = new_motion_plan[2]
    elif idx_t == transn_idx[3]: motion_plan[3] = new_motion_plan[3]
    else: isReceived = isReceived - 1

def get_motor_angles(motion_plan, idx_t):
    global motor_angles
    motor_angles[0] = motion_plan[0][(idx_t+leg_offset[0])%n]
    motor_angles[1] = motion_plan[1][(idx_t+leg_offset[0])%n]
    motor_angles[2] = motion_plan[0][(idx_t+leg_offset[1])%n]
    motor_angles[3] = motion_plan[1][(idx_t+leg_offset[1])%n]
    motor_angles[4] = motion_plan[2][(idx_t+leg_offset[2])%n]
    motor_angles[5] = motion_plan[3][(idx_t+leg_offset[2])%n]
    motor_angles[6] = motion_plan[2][(idx_t+leg_offset[3])%n]
    motor_angles[7] = motion_plan[3][(idx_t+leg_offset[3])%n]


if __name__ == '__main__':

    cmd_vel_listener()
    #check_connection()                          #Uncomment motor_handler line 102
    motion_plan = solver()
    idx_t = int(0.625*n)
    get_motor_angles(motion_plan, idx_t)
    #move_motors()

    while not rospy.is_shutdown():
        #start_time = time.time()
        if isChanged:
            new_motion_plan = solver()
            isChanged = False
            isReceived = 0

        if isReceived != 4:
            change_motion_plan(idx_t, motion_plan, new_motion_plan)


        get_motor_angles(motion_plan, idx_t)
        #write_motor_angles()
        #time.sleep(step_size)
        idx_t = (idx_t+1)%n

        #print("--- %s seconds ---" % (time.time() - start_time))

    handler.close_port()

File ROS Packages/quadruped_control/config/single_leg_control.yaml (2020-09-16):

single_leg:
  # Publish all joint states -----------------------------------
  joint_state_controller:
    type: joint_state_controller/JointStateController
    publish_rate: 50

  # Position Controllers ---------------------------------------
  motor_1_position_controller:
    type: effort_controllers/JointPositionController
    joint: motor_1
    pid: {p: 100.0, i: 0.01, d: 1}
  motor_2_position_controller:
    type: effort_controllers/JointPositionController
    joint: motor_2
    pid: {p: 100.0, i: 0.01, d: 1}

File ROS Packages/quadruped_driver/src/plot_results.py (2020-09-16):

#!/usr/bin/env python

import os
import tf
import numpy as np
import matplotlib.pyplot as plt
from geometry_msgs.msg import Quaternion
import csv

test_name = "straight_line2"

dir = os.path.join("/home/arjun/quadruped_ws/src/quadruped_driver/results_csvs", test_name)
if not os.path.isdir(dir):
    print ("Directory does Not Exist")
    exit()

def read_csv(filename):
    rows = []
    with open(filename, 'r') as csvfile:
    	csvreader = csv.reader(csvfile, quoting=csv.QUOTE_NONNUMERIC)
    	for row in csvreader:
    		rows.append(row)

    return np.array(rows, dtype=float)

def get_desired(sim_time, twist, ground_truth):
    '''quat = Quaternion()
    quat.x = ground_truth[0,4]; quat.x = ground_truth[0,5]; quat.x = ground_truth[0,6]; quat.x = ground_truth[0,7]'''
    quat = ground_truth[0,4:]
    rpy = tf.transformations.euler_from_quaternion(quat)
    phi = rpy[2]
    t = np.arange(0, sim_time[0,1]-sim_time[0,0], 0.01).reshape(-1,1)
    if twist[0,1]!=0:
        R = twist[0,0]/(0.6*twist[0,1]) ##################################
        C = ground_truth[0,1:3] - np.array([R*np.sin(phi), -R*np.cos(phi)]).reshape(1,2)
        C2 = C
        a = np.hstack((np.cos(twist[0,1]*t[:,0] + phi-np.pi/2).reshape(-1,1), np.sin(twist[0,1]*t[:,0] + phi-np.pi/2).reshape(-1,1)))
        traj = C2 + R*a
        traj2 = C2 + 0.05*a
        o = phi + 0.36*t*twist[0,1]
    else:
        traj = ground_truth[0,1:3] + t[:,0].reshape(-1,1)*twist[0,0]*np.array([np.cos(phi), np.sin(phi)]).reshape(1,2)
        o = phi*np.ones(t.shape)

    traj = np.concatenate((traj.reshape(-1,2), o), axis=1)
    return traj

def show_plots(sim_time, desired, ground_truth):
    fig = plt.figure()
    ax  = fig.add_subplot(111)
    maxx = np.max(np.concatenate((desired[:,0], ground_truth[:,1])))
    maxy = np.max(np.concatenate((desired[:,1], ground_truth[:,2])))
    minx = np.min(np.concatenate((desired[:,0], ground_truth[:,1])))
    miny = np.min(np.concatenate((desired[:,1], ground_truth[:,2])))
    ax.plot(desired[:,0],desired[:,1], 'r')
    ax.plot(ground_truth[:,1],ground_truth[:,2], 'b')
    plt.xlim(minx-0.1, maxx+0.1)
    plt.ylim(miny-0.1, maxy+0.1)
    plt.gca().set_aspect('equal', adjustable='datalim')
    plt.legend(('Desired', 'Actual'))
    plt.title("Trajectory")
    plt.xlabel("x (m)")
    plt.ylabel("y (m)")
    plt.show()

    rpy = np.zeros((ground_truth.shape[0],3))
    for i in range(ground_truth.shape[0]):
        rpy[i,:] = tf.transformations.euler_from_quaternion(ground_truth[i,4:])
    phi = (180*rpy[:,2]/np.pi)%360
    desired[:,2] = (180*desired[:,2]/np.pi)%360
    t_des = np.arange(0, sim_time[0,1]-sim_time[0,0], 0.01).reshape(-1,1)
    t = ground_truth[:,0].reshape(-1,1) - ground_truth[0,0]
    maxy = max(np.max(phi[:]), np.max(desired[:,2]))
    miny = min(np.min(phi[:]), np.min(desired[:,2]))
    plt.plot(t_des, desired[:,2] ,'r', t, phi, 'b')
    plt.xlim(0, t[-1,0])
    plt.ylim(miny-5, maxy+5)
    plt.legend(('Desired', 'Actual'))
    plt.title("Orientation")
    plt.ylabel("${\Theta}$ (deg)")
    plt.xlabel("time (s)")
    plt.show()

    fig = plt.figure()
    ax  = fig.add_subplot(111)
    mn = np.mean(ground_truth[:,3])
    t = ground_truth[:,0].reshape(-1,1) - ground_truth[0,0]
    des = mn*np.zeros(ground_truth[:,0].shape)
    maxy = np.max(ground_truth[:,3]-mn)
    miny = np.min(ground_truth[:,3]-mn)
    ax.plot(t, des ,'r',linewidth=3.0)
    ax.plot(t, ground_truth[:,3]-mn, 'b', t, des-0.005 ,'--y', t, des+0.005 ,'--y')
    plt.xlim(0, t[-1,0])
    plt.ylim(miny-0.01, maxy+0.01)
    ax.legend(('Desired', 'Actual'))
    plt.title("COM Stability")
    plt.ylabel("z (m)")
    plt.xlabel("time (s)")
    plt.show()

    print("Done!")

if __name__ == '__main__':
    twist = read_csv(os.path.join(dir, "twist.csv")).reshape(1,2)
    sim_time = read_csv(os.path.join(dir, "sim_time.csv")).reshape(1,2)
    ground_truth = read_csv(os.path.join(dir, "ground_truth.csv"))
    desired = get_desired(sim_time, twist, ground_truth)

    show_plots(sim_time, desired, ground_truth)

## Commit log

2020-09-16 Added Matlab Codes and CAD Files
    [Bracket-Horn - Copy.SLDPRT, Bracket-Horn.SLDPRT, Channel_1.SLDPRT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]
2020-09-16 Added Simulation Results
    [actual_traj.xlsx, desired_traj.xlsx, ground_truth.xlsx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]
